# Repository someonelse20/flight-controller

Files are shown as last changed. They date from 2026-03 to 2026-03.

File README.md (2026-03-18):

# Custom Flight Controller

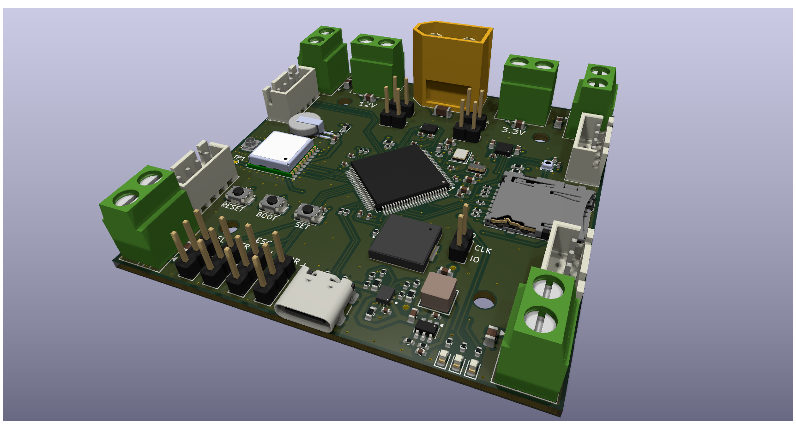
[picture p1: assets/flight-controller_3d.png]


A custom flight controller with IMU sensors for orientation, a GPS module, a Micro SD card slot, and support for my LoRa Transceiver module for telemetry along with a custom flight controller algorithm.
I built this for my project of creating a custom drone from scratch. 

## Usage
To use plug in a 3 cell lipo battery into the XT60 connector and attach the ESCs to the 4 corner screw terminals. Then plug in the ESC headers into the coresponding ESC headers on the board. 
Make sure a GPS antenna is connected to the U.FL connector. Plug in my transceiver module into any of the UART headers.
A Micro SD card is not strictly required but if inserted the board will log data and error logs. 

## Project Images
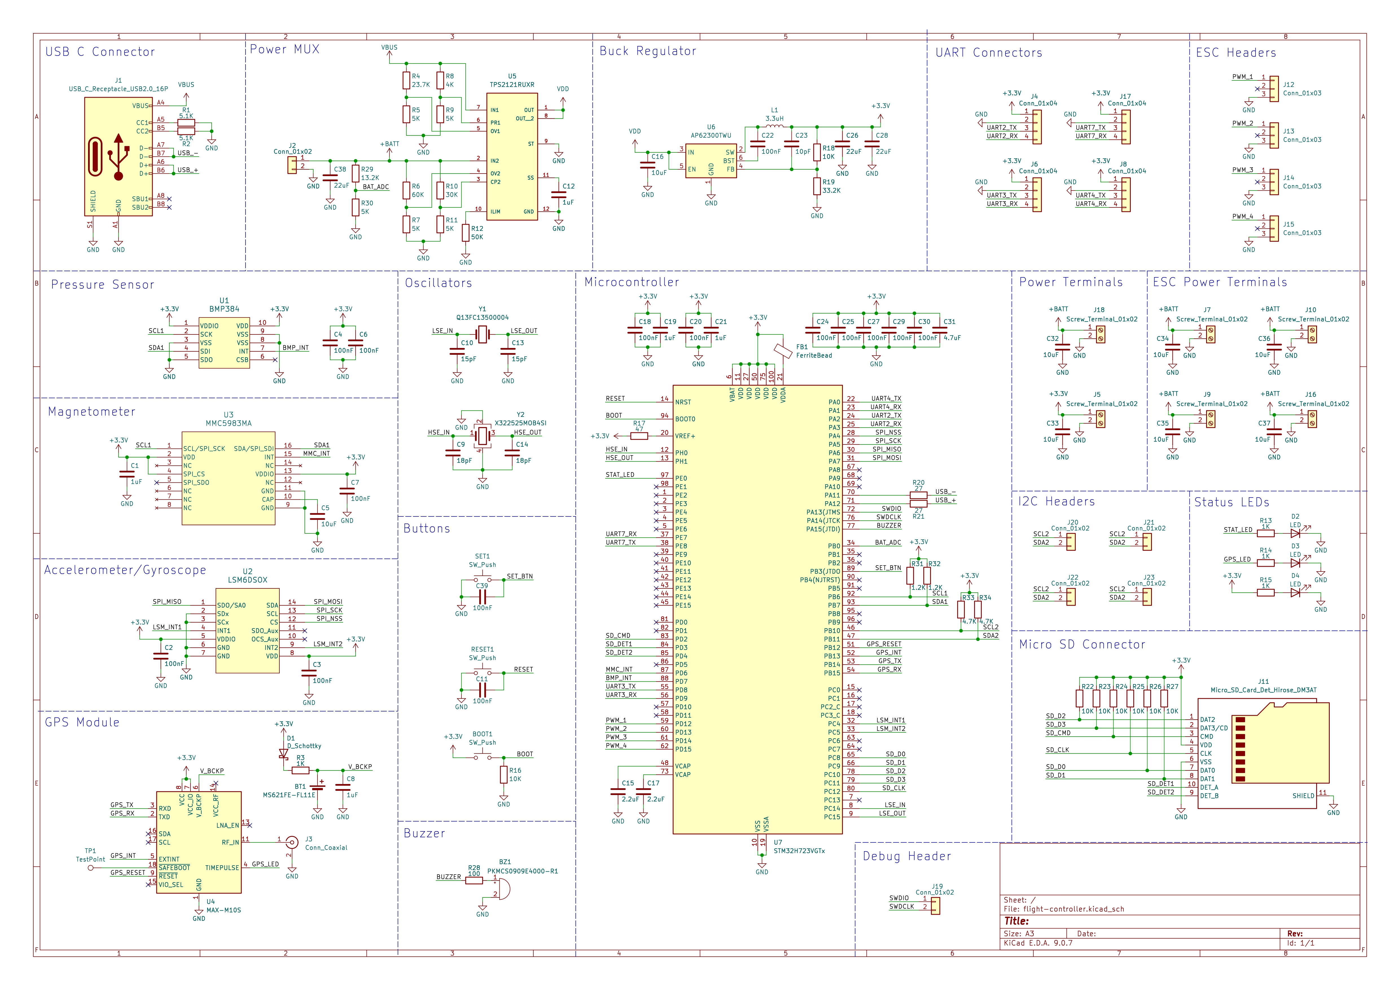
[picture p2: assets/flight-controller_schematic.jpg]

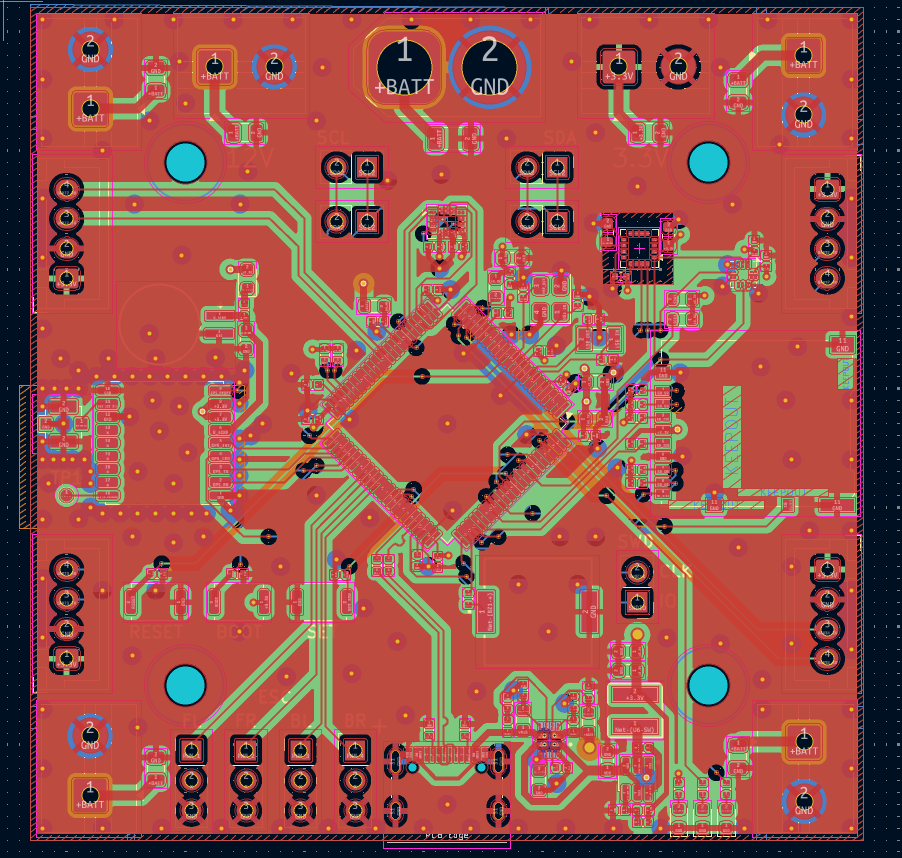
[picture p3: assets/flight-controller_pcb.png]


## BOM
The full BOM from digikey is in the digikey-bom.csv file in production.

| PCB Assembly | JLCPCB  | 96.10 | https://jlcpcb.com |
|---|---|---|---|
| Hand Soldered Parts | Digikey | 67.30 | https://www.digikey.com/en/mylists/list/OHMGL71TDV |

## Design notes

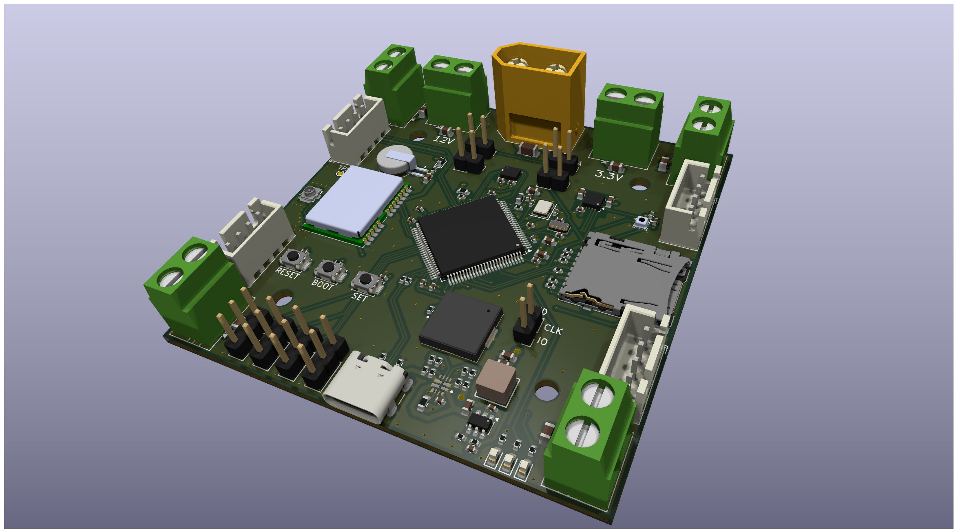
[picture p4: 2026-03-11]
hardware/flight-controller-3d.png

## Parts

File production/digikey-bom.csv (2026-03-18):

Index | Manufacturer Part Number | Manufacturer Name | Description | Quantity | Product Link
1 | MS621FE-FL11E | Seiko Instruments | BATT LITHIUM 3V 5.5MAH COIN | 2 | https://www.digikey.com/en/products/detail/seiko-instruments/MS621FE-FL11E/1889208
2 | MAX-M10S-00B | u-blox | GNSS LCC RX, ROM, TCXO, LNA, SAW | 2 | https://www.digikey.com/en/products/detail/u-blox/MAX-M10S-00B/15712906
3 | 691137710002 | Würth Elektronik | TERM BLK 2POS SIDE ENTRY 5MM PCB | 10 | https://www.digikey.com/en/products/detail/w%C3%BCrth-elektronik/691137710002/6644051
4 | FIT0587 | DFRobot | HIGH QUALITY GOLD PLATED XT60 MA | 2 | https://www.digikey.com/en/products/detail/dfrobot/FIT0587/9559256
5 | LSM6DSOXTR | STMicroelectronics | INEMO INERTIAL MODULE: 3D ACCELE | 2 | https://www.digikey.com/en/products/detail/stmicroelectronics/LSM6DSOXTR/9841882
6 | MMC5983MA | Memsic Inc. | SEN MR I2C/SPI 16-LGA | 2 | https://www.digikey.com/en/products/detail/memsic-inc/MMC5983MA/10452795
7 | BMP384 | Bosch Sensortec | SENSOR 18.13PSIA 10LGA | 2 | https://www.digikey.com/en/products/detail/bosch-sensortec/BMP384/13681277
8 | U.FL-R-SMT-1(10) | Hirose Electric Co Ltd | CONN U.FL RCPT STR 50 OHM SMD | 2 | https://www.digikey.com/en/products/detail/hirose-electric-co-ltd/U-FL-R-SMT-1-10/2391570
9 | B4B-XH-A | JST Sales America Inc. | CONN HEADER VERT 4POS 2.5MM | 10 | https://www.digikey.com/en/products/detail/jst-sales-america-inc/B4B-XH-A/1651047
10 | FXUB66.07.0150C | Taoglas Limited | RF ANT 3.4GHZ FLAT PATCH U.FL | 2 | https://www.digikey.com/en/products/detail/taoglas-limited/FXUB66-07-0150C/3724559

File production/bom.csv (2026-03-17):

Designator | Footprint | Quantity | Value | LCSC Part #
BOOT1, RESET1, SET1 | SW_Push_SPST_NO_Alps_SKRK | 3 | SW_Push
BT1 | BAT_MS621FE-FL11E | 1 | MS621FE-FL11E
BZ1 | SPKR_PKMCS0909E4000-R1 | 1 | PKMCS0909E4000-R1
C1, C19, C21, C8 | 0603 | 4 | 1uF
C10, C13 | 0402 | 2 | 15pF
C11, C18, C2, C20, C22, C24, C25, C27, C29, C3, C30, C39, C4, C6, C7 | 0402 | 15 | 100nF
C12 | 0402 | 1 | 1uF
C14, C9 | 0402 | 2 | 18pF
C15, C17 | 0402 | 2 | 2.2uF
C16, C5 | 0603 | 2 | 10uF
C23 | 0402 | 1 | 10pF
C26, C28 | 0603 | 2 | 22uF
C31 | 0603 | 1 | 4.7uF
C32, C33, C34, C35, C36, C37 | 0805 | 6 | 10uF
C38 | 1206 | 1 | 22uF
D1 | 0603 | 1 | D_Schottky
D2, D3 | 0603 | 2 | LED
D4 | 0603 | 1 | LED
FB1 | 0603 | 1 | FerriteBead
J1 | USB_C_Receptacle_GCT_USB4105-xx-A_16P_TopMnt_Horizontal | 1 | USB_C_Receptacle_USB2.0_16P
J10, J16, J18, J5, J7, J9 | TerminalBlock_MaiXu_MX126-5.0-02P_1x02_P5.00mm | 6 | Screw_Terminal_01x02
J11 | microSD_HC_Hirose_DM3AT-SF-PEJM5 | 1 | Micro_SD_Card_Det_Hirose_DM3AT
J12, J13, J14, J15 | PinHeader_1x03_P2.54mm_Vertical | 4 | Conn_01x03
J17, J4, J6, J8 | JST_XH_B4B-XH-A_1x04_P2.50mm_Vertical | 4 | Conn_01x04
J19, J20, J21, J22, J23 | PinHeader_1x02_P2.54mm_Vertical | 5 | Conn_01x02
J2 | AMASS_XT60-M_1x02_P7.20mm_Vertical | 1 | Conn_01x02
J3 | U.FL_Molex_MCRF_73412-0110_Vertical | 1 | Conn_Coaxial
L1 | IND_SRP4030FA_BRN | 1 | 3.3uH
R1, R2 | 0402 | 2 | 5.1K
R10 | 0402 | 1 | 30K
R11, R30, R5, R7, R9 | 0402 | 5 | 5K
R12 | 0603 | 1 | 50K
R13, R14, R15, R3 | 0402 | 4 | 1K
R16, R18, R22, R23, R24, R25, R26, R27 | 0402 | 8 | 10K
R17 | 0402 | 1 | 47
R19 | 0402 | 1 | 33.2K
R20, R21 | 0402 | 2 | 27
R28 | 0402 | 1 | 100
R29 | 0603 | 1 | 13.2K
R31, R32 | 0603 | 2 | 1.2K
R33, R34 | 0402 | 2 | 4.7K
R4 | 0402 | 1 | 23.7K
R6 | 0603 | 1 | 60K
R8 | 0603 | 1 | 4K
U1 | Rohm_MLGA010V020A_LGA-10_2x2mm_P0.45mm_LayoutBorder2x3y | 1 | BMP384
U2 | LGA-14_3x2.5mm_P0.5mm_LayoutBorder3x4y | 1 | LSM6DSOTR
U3 | LGA-16_3x3mm_P0.5mm | 1 | MMC5983MA
U4 | ublox_MAX | 1 | MAX-M10S
U5 | IC_TPS2121RUXR | 1 | TPS2121RUXR
U6 | TSOT-23-6 | 1 | AP62300TWU
U7 | LQFP-100_14x14mm_P0.5mm | 1 | STM32H723VGTx
Y1 | Crystal_SMD_3215-2Pin_3.2x1.5mm | 1 | Q13FC13500004
Y2 | Crystal_SMD_3225-4Pin_3.2x2.5mm | 1 | X322525MOB4SI

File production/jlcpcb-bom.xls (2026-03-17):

JLCPCB BOM Tool - BOM Matching
BOM name：jlcpcb-bom-JLCPCB Assembly Order.xlsx |  |  | Download Time：2026-03-18 00:47:03 |  |  |  | * Our matching results are updated in real-time, but stock and prices may change. If it's been over 24 hours, please re-match before placing your order.
PCB Assembled Qty：5 |  |  | Est. Total Price：25.3142
Your BOM |  |  |  |  | Matched Parts |  |  |  |  |  |  | Order Information
Top Designator | Bottom Designator | Comment | Footprint | JLCPCB Part # | Matches | Part # | Manufacturer | Footprint | Description | Category | Warning | JLCPCB Part # | Product link | Lib Type | Qty | Source | Total Price ($)
BOOT1,RESET1,SET1 |  | SW_Push | SMD,4x3mm |  | Unconfirmed | TS-1088-AR02016 | XUNPU | SMD,4x3mm | -30℃~+80℃ 1.6N 100,000 cycles 12V 2mm 3mm 4mm 50mA Black Round Button SMD(SMT) Tab SPST Surface Mount,Vertical Without Bracket SMD,4x3mm Tactile Switches ROHS | Tactile Switches | 1.There may be multiple types of parts, but one type of part has been matched. Please check.; | C720477 | https://jlcpcb.com/partdetail/XUNPU-TS_1088AR02016/C720477 | Basic | 6 | 6 JLCPCB | 0.3252
BZ1 |  | PKMCS0909E4000-R1 | - |  | Select by System | PKMCS0909E4000-R1 | Murata Electronics | - | -40℃~+85℃ 1.9mm 12.5V 4kHz 65dB 9mm 9mm Passive (Externally Driven) Piezoelectric - Buzzers ROHS | Buzzers |  | C910763 | https://jlcpcb.com/partdetail/MurataElectronics-PKMCS0909E4000R1/C910763 | Extended | 2 | 2 JLCPCB | 1.5874
C1,C19,C21,C8 |  | 1uF | 0603 |  | Select by System | CL10A105KB8NNNC | Samsung Electro-Mechanics | 0603 | 1uF 50V X5R ±10% 0603 Multilayer Ceramic Capacitors MLCC - SMD/SMT ROHS | Multilayer Ceramic Capacitors MLCC - SMD/SMT |  | C15849 | https://jlcpcb.com/partdetail/16531-CL10A105KB8NNNC/C15849 | Basic | 8 | 8 JLCPCB | 0.0576
C10,C13 |  | 15pF | 0402 |  | Select by System | 0402CG150J500NT | FH (Guangdong Fenghua Advanced Tech) | 0402 | 15pF 50V C0G ±5% 0402 Multilayer Ceramic Capacitors MLCC - SMD/SMT ROHS | Multilayer Ceramic Capacitors MLCC - SMD/SMT |  | C1548 | https://jlcpcb.com/partdetail/1900-0402CG150J500NT/C1548 | Basic | 4 | 4 JLCPCB | 0.0052
C11,C18,C2,C20,C22,C24,C25,C27,C29,C3,C30,C39,C4,C6,C7 |  | 100nF | 0402 |  | Select by System | CL05B104KO5NNNC | Samsung Electro-Mechanics | 0402 | 100nF 16V X7R ±10% 0402 Multilayer Ceramic Capacitors MLCC - SMD/SMT ROHS | Multilayer Ceramic Capacitors MLCC - SMD/SMT |  | C1525 | https://jlcpcb.com/partdetail/1877-CL05B104KO5NNNC/C1525 | Basic | 30 | 30 JLCPCB | 0.039
C12 |  | 1uF | 0402 |  | Select by System | CL05A105KA5NQNC | Samsung Electro-Mechanics | 0402 | 1uF 25V X5R ±10% 0402 Multilayer Ceramic Capacitors MLCC - SMD/SMT ROHS | Multilayer Ceramic Capacitors MLCC - SMD/SMT |  | C52923 | https://jlcpcb.com/partdetail/53938-CL05A105KA5NQNC/C52923 | Basic | 2 | 2 JLCPCB | 0.0082
C14,C9 |  | 18pF | 0402 |  | Select by System | 0402CG180J500NT | FH (Guangdong Fenghua Advanced Tech) | 0402 | 18pF 50V C0G ±5% 0402 Multilayer Ceramic Capacitors MLCC - SMD/SMT ROHS | Multilayer Ceramic Capacitors MLCC - SMD/SMT |  | C1549 | https://jlcpcb.com/partdetail/1901-0402CG180J500NT/C1549 | Basic | 4 | 4 JLCPCB | 0.0048
C15,C17 |  | 2.2uF | 0402 |  | Select by System | CL05A225MQ5NSNC | Samsung Electro-Mechanics | 0402 | 2.2uF 6.3V X5R ±20% 0402 Multilayer Ceramic Capacitors MLCC - SMD/SMT ROHS | Multilayer Ceramic Capacitors MLCC - SMD/SMT |  | C12530 | https://jlcpcb.com/partdetail/13164-CL05A225MQ5NSNC/C12530 | Basic | 4 | 4 JLCPCB | 0.0104
C16,C5 |  | 10uF | 0603 |  | Select by System | CL10A106KP8NNNC | Samsung Electro-Mechanics | 0603 | 10V 10uF X5R ±10% 0603 Multilayer Ceramic Capacitors MLCC - SMD/SMT ROHS | Multilayer Ceramic Capacitors MLCC - SMD/SMT |  | C19702 | https://jlcpcb.com/partdetail/20411-CL10A106KP8NNNC/C19702 | Basic | 4 | 4 JLCPCB | 0.0288
C23 |  | 10pF | 0402 |  | Select by System | CL05C100JB5NNNC | Samsung Electro-Mechanics | 0402 | 10pF 50V C0G ±5% 0402 Multilayer Ceramic Capacitors MLCC - SMD/SMT ROHS | Multilayer Ceramic Capacitors MLCC - SMD/SMT |  | C32949 | https://jlcpcb.com/partdetail/33914-CL05C100JB5NNNC/C32949 | Basic | 2 | 2 JLCPCB | 0.009
C26,C28 |  | 22uF | 0603 |  | Select by System | CL10A226MQ8NRNC | Samsung Electro-Mechanics | 0603 | 22uF 6.3V X5R ±20% 0603 Multilayer Ceramic Capacitors MLCC - SMD/SMT ROHS | Multilayer Ceramic Capacitors MLCC - SMD/SMT |  | C59461 | https://jlcpcb.com/partdetail/60514-CL10A226MQ8NRNC/C59461 | Basic | 4 | 4 JLCPCB | 0.0376
C31 |  | 4.7uF | 0603 |  | Select by System | CL10A475KO8NNNC | Samsung Electro-Mechanics | 0603 | 16V 4.7uF X5R ±10% 0603 Multilayer Ceramic Capacitors MLCC - SMD/SMT ROHS | Multilayer Ceramic Capacitors MLCC - SMD/SMT |  | C19666 | https://jlcpcb.com/partdetail/20375-CL10A475KO8NNNC/C19666 | Basic | 2 | 2 JLCPCB | 0.0206
C32,C33,C34,C35,C36,C37 |  | 10uF | 0805 |  | Select by System | GRM21BR61H106KE43L | Murata Electronics | 0805 | 10uF 50V X5R ±10% 0805 Multilayer Ceramic Capacitors MLCC - SMD/SMT ROHS | Multilayer Ceramic Capacitors MLCC - SMD/SMT |  | C440198 | https://jlcpcb.com/partdetail/439567-GRM21BR61H106KE43L/C440198 | Basic | 12 | 12 JLCPCB | 0.8604
C38 |  | 22uF | 1206 |  | Select by System | CL31A226KAHNNNE | Samsung Electro-Mechanics | 1206 | 22uF 25V X5R ±10% 1206 Multilayer Ceramic Capacitors MLCC - SMD/SMT ROHS | Multilayer Ceramic Capacitors MLCC - SMD/SMT |  | C12891 | https://jlcpcb.com/partdetail/13537-CL31A226KAHNNNE/C12891 | Basic | 2 | 2 JLCPCB | 0.0946
D1 |  | D_Schottky | 0603 |  | Select by System | SD0603S040S0R2 | Kyocera AVX | 0603 | 1uA@40V 200mA 40V 450mV@200mA 0603 Schottky Diodes ROHS | Schottky Diodes |  | C143772 | https://jlcpcb.com/partdetail/KyoceraAVX-SD0603S040S0R2/C143772 | Extended | 5 | 5 JLCPCB | 0.8985
D2,D3 |  | LED | 0603 |  | Select by System | KT-0603W | Hubei KENTO Elec | 0603 | -40℃~+85℃ 100mW 120° 2.6V~3.1V 360mcd 5mA Discrete Diode Top-mount White Yellow Lens 0603 LED Indication - Discrete ROHS | LED Indication - Discrete |  | C2290 | https://jlcpcb.com/partdetail/Hubei_KENTOElec-KT0603W/C2290 | Basic | 4 | 4 JLCPCB | 0.0468
D4 |  | LED | 0603 |  | Select by System | KT-0603R | Hubei KENTO Elec | 0603 | -40℃~+85℃ 120° 2.4V 20mA 300mcd 40mW 615nm~630nm 645nm Discrete Diode Red Water Clear 0603 LED Indication - Discrete ROHS | LED Indication - Discrete |  | C2286 | https://jlcpcb.com/partdetail/Hubei_KENTOElec-KT0603R/C2286 | Basic | 2 | 2 JLCPCB | 0.013
FB1 |  | FerriteBead | 0603 |  | Select by System | GZ1608D601TF | Sunlord | 0603 | -55℃~+125℃ 1 200mA 450mΩ 600Ω@100MHz ±25% 0603 Ferrite Beads ROHS | Ferrite Beads |  | C1002 | https://jlcpcb.com/partdetail/Sunlord-GZ1608D601TF/C1002 | Basic | 2 | 2 JLCPCB | 0.0264
J1 |  | USB_C_Receptacle_USB2.0_16P | SMD |  | Select by System | TYPE-C-31-M-12 | Korean Hroparts Elec | SMD | -30℃~+80℃ 1 10,000 cycles 16P 20V 5A 7.35mm Female Surface Mount, Right Angle Type-C SMD USB Connectors ROHS | USB Connectors |  | C165948 | https://jlcpcb.com/partdetail/Korean_HropartsElec-TYPE_C_31_M12/C165948 | Extended | 2 | 2 JLCPCB | 0.3632
J11 |  | Micro_SD_Card_Det_Hirose_DM3AT | SMD |  | Select by System | DM3AT-SF-PEJM5 | HRS(Hirose) | SMD | -25℃~+85℃ 1.68mm Connector and Ejector MicroSD Card (TF Card) No Push-Push SMD SD Card / Memory Card Connector ROHS | SD Card / Memory Card Connector |  | C114218 | https://jlcpcb.com/partdetail/HRS_Hirose-DM3AT_SFPEJM5/C114218 | Extended | 2 | 2 JLCPCB | 2.7756
L1 |  | 3.3uH | SMD,4x4mm |  | Select by System | SWPA4030S3R3MT | Sunlord | SMD,4x4mm | 2.4A 3.3uH 3.6A 52mΩ ±20% SMD,4x4mm Power Inductors ROHS | Power Inductors |  | C15269 | https://jlcpcb.com/partdetail/Sunlord-SWPA4030S3R3MT/C15269 | Extended | 6 | 6 JLCPCB | 0.4842
R1,R2 |  | 5.1K | 0402 |  | Select by System | 0402WGF5101TCE | UNI-ROYAL(Uniroyal Elec) | 0402 | -55℃~+155℃ 5.1kΩ 50V 62.5mW Thick Film Resistor ±1% ±100ppm/℃ 0402 Chip Resistor - Surface Mount ROHS | Chip Resistor - Surface Mount |  | C25905 | https://jlcpcb.com/partdetail/26648-0402WGF5101TCE/C25905 | Basic | 4 | 4 JLCPCB | 0.0032
R4 |  | 23.7K | 0402 |  | Select by System | 0402WGF2372TCE | UNI-ROYAL(Uniroyal Elec) | 0402 | -55℃~+155℃ 23.7kΩ 50V 62.5mW Thick Film Resistor ±1% ±100ppm/℃ 0402 Chip Resistor - Surface Mount ROHS | Chip Resistor - Surface Mount |  | C82134 | https://jlcpcb.com/partdetail/83289-0402WGF2372TCE/C82134 | Extended | 20 | 20 JLCPCB | 0.014
R6 |  | 60K | 0603 |  | Select by System | RT0603BRD0760KL | YAGEO | 0603 | -55℃~+155℃ 100mW 60kΩ 75V Thin Film Resistor ±0.1% ±25ppm/℃ 0603 Chip Resistor - Surface Mount ROHS | Chip Resistor - Surface Mount |  | C6460576 | https://jlcpcb.com/partdetail/YAGEO-RT0603BRD0760KL/C6460576 | Extended | 20 | 20 JLCPCB | 0.526
R8 |  | 4K | 0603 |  | Select by System | ARG03FTC4001N | Viking Tech | 0603 | -55℃~+155℃ 100mW 4kΩ 75V Thin Film Resistor ±1% ±25ppm/℃ 0603 Chip Resistor - Surface Mount ROHS | Chip Resistor - Surface Mount |  | C2984443 | https://jlcpcb.com/partdetail/VikingTech-ARG03FTC4001N/C2984443 | Extended | 20 | 20 JLCPCB | 0.168
R10 |  | 30K | 0402 |  | Select by System | FRC0402F3002TS | FOJAN | 0402 | -55℃~+155℃ 30kΩ 50V 62.5mW Thick Film Resistor ±1% ±100ppm/℃ 0402 Chip Resistor - Surface Mount ROHS | Chip Resistor - Surface Mount |  | C2909347 | https://jlcpcb.com/partdetail/FOJAN-FRC0402F3002TS/C2909347 | Extended | 20 | 20 JLCPCB | 0.012
R11,R30,R5,R7,R9 |  | 5K | 0402 |  | Select by System | RC0402FR-075KL | YAGEO | 0402 | -55℃~+155℃ 50V 5kΩ 62.5mW Thick Film Resistor ±1% ±100ppm/℃ 0402 Chip Resistor - Surface Mount ROHS | Chip Resistor - Surface Mount |  | C477765 | https://jlcpcb.com/partdetail/YAGEO-RC0402FR075KL/C477765 | Extended | 20 | 20 JLCPCB | 0.016
R12 |  | 50K | 0603 |  | Select by System | RT0603BRD0750KL | YAGEO | 0603 | -55℃~+155℃ 100mW 50kΩ 75V Thin Film Resistor ±0.1% ±25ppm/℃ 0603 Chip Resistor - Surface Mount ROHS | Chip Resistor - Surface Mount |  | C861451 | https://jlcpcb.com/partdetail/YAGEO-RT0603BRD0750KL/C861451 | Extended | 20 | 20 JLCPCB | 0.488
R13,R14,R15,R3 |  | 1K | 0402 |  | Select by System | 0402WGF1001TCE | UNI-ROYAL(Uniroyal Elec) | 0402 | -55℃~+155℃ 1kΩ 50V 62.5mW Thick Film Resistor ±1% ±100ppm/℃ 0402 Chip Resistor - Surface Mount ROHS | Chip Resistor - Surface Mount |  | C11702 | https://jlcpcb.com/partdetail/12256-0402WGF1001TCE/C11702 | Basic | 8 | 8 JLCPCB | 0.0056
R16,R18,R22,R23,R24,R25,R26,R27 |  | 10K | 0402 |  | Select by System | 0402WGF1002TCE | UNI-ROYAL(Uniroyal Elec) | 0402 | -55℃~+155℃ 10kΩ 50V 62.5mW Thick Film Resistor ±1% ±100ppm/℃ 0402 Chip Resistor - Surface Mount ROHS | Chip Resistor - Surface Mount |  | C25744 | https://jlcpcb.com/partdetail/26487-0402WGF1002TCE/C25744 | Basic | 16 | 16 JLCPCB | 0.0128
R17 |  | 47 | 0402 |  | Select by System | 0402WGF470JTCE | UNI-ROYAL(Uniroyal Elec) | 0402 | -55℃~+155℃ 47Ω 50V 62.5mW Thick Film Resistor ±1% ±100ppm/℃ 0402 Chip Resistor - Surface Mount ROHS | Chip Resistor - Surface Mount |  | C25118 | https://jlcpcb.com/partdetail/25861-0402WGF470JTCE/C25118 | Extended | 20 | 20 JLCPCB | 0.016
R19 |  | 33.2K | 0402 |  | Select by System | FRC0402F3322TS | FOJAN | 0402 | -55℃~+155℃ 33.2kΩ 50V 62.5mW Thick Film Resistor ±1% ±100ppm/℃ 0402 Chip Resistor - Surface Mount ROHS | Chip Resistor - Surface Mount |  | C2930001 | https://jlcpcb.com/partdetail/FOJAN-FRC0402F3322TS/C2930001 | Extended | 20 | 20 JLCPCB | 0.012
R20,R21 |  | 27 | 0402 |  | Select by System | 0402WGF270JTCE | UNI-ROYAL(Uniroyal Elec) | 0402 | -55℃~+155℃ 27Ω 50V 62.5mW Thick Film Resistor ±1% ±100ppm/℃ 0402 Chip Resistor - Surface Mount ROHS | Chip Resistor - Surface Mount |  | C25100 | https://jlcpcb.com/partdetail/25843-0402WGF270JTCE/C25100 | Extended | 20 | 20 JLCPCB | 0.016
R28 |  | 100 | 0402 |  | Select by System | 0402WGF1000TCE | UNI-ROYAL(Uniroyal Elec) | 0402 | -55℃~+155℃ 100Ω 50V 62.5mW Thick Film Resistor ±1% ±100ppm/℃ 0402 Chip Resistor - Surface Mount ROHS | Chip Resistor - Surface Mount |  | C25076 | https://jlcpcb.com/partdetail/25819-0402WGF1000TCE/C25076 | Basic | 2 | 2 JLCPCB | 0.0016
R29 |  | 13.2K | 0603 |  | Select by System | RT0603BRD0713K2L | YAGEO | 0603 | -55℃~+155℃ 100mW 13.2kΩ 75V Thin Film Resistor ±0.1% ±25ppm/℃ 0603 Chip Resistor - Surface Mount ROHS | Chip Resistor - Surface Mount |  | C861116 | https://jlcpcb.com/partdetail/YAGEO-RT0603BRD0713K2L/C861116 | Extended | 20 | 20 JLCPCB | 0.518
R31,R32 |  | 1.2K | 0603 |  | Select by System | 0603WAF1201T5E | UNI-ROYAL(Uniroyal Elec) | 0603 | -55℃~+155℃ 1.2kΩ 100mW 75V Thick Film Resistor ±1% ±100ppm/℃ 0603 Chip Resistor - Surface Mount ROHS | Chip Resistor - Surface Mount |  | C22765 | https://jlcpcb.com/partdetail/23492-0603WAF1201T5E/C22765 | Basic | 4 | 4 JLCPCB | 0.0068
R33,R34 |  | 4.7K | 0402 |  | Select by System | 0402WGF4701TCE | UNI-ROYAL(Uniroyal Elec) | 0402 | -55℃~+155℃ 4.7kΩ 50V 62.5mW Thick Film Resistor ±1% ±100ppm/℃ 0402 Chip Resistor - Surface Mount ROHS | Chip Resistor - Surface Mount |  | C25900 | https://jlcpcb.com/partdetail/26643-0402WGF4701TCE/C25900 | Basic | 4 | 4 JLCPCB | 0.0032
U1 |  | BMP384 | LGA-10(2x2) |  | Select by System | BMP384 | Bosch Sensortec | LGA-10(2x2) | -40℃~+85℃ 1.65V~3.6V 1pa/K 2uA 30Kpa~1.25bar 50pa 9pa I2C、SPI LGA-10(2x2) Pressure Sensors ROHS | Pressure Sensors |  | C5577555 | https://jlcpcb.com/partdetail/BoschSensortec-BMP384/C5577555 | Extended | 0 | 0 JLCPCB | 0
U2 |  | LSM6DSOTR | LGA-14(2.5x3) |  | Select by System | LSM6DSOTR | STMicroelectronics | LGA-14(2.5x3) | -40℃~+85℃ 1.71V~3.6V 9KB Accelerometer Gyroscope SPI、I2C X,Y,Z X,Y,Z ±16g ±2000dps LGA-14(2.5x3) Accelerometers ROHS | Accelerometers |  | C2655100 | https://jlcpcb.com/partdetail/STMicroelectronics-LSM6DSOTR/C2655100 | Extended | 0 | 0 JLCPCB | 0
U3 |  | MMC5983MA | LGA-16(3x3) |  | Select by System | MMC5983MA | MEMSIC | LGA-16(3x3) | -40℃~+105℃ 18bit 2.8V~3.6V 450uA I2C、SPI ±8Gs ±8Gs LGA-16(3x3) 3D Magnetic Sensors ROHS | 3D Magnetic Sensors |  | C404329 | https://jlcpcb.com/partdetail/MEMSIC-MMC5983MA/C404329 | Extended | 0 | 0 JLCPCB | 0
U5 |  | TPS2121RUXR | VQFN-HR-12(2x2.5) |  | Select by System | TPS2121RUXR | Texas Instruments | VQFN-HR-12(2x2.5) | -40℃~+125℃ 2.8V~22V 200uA 56mΩ VQFN-HR-12(2x2.5) ORing Controllers ROHS | Battery Management |  | C485916 | https://jlcpcb.com/partdetail/TexasInstruments-TPS2121RUXR/C485916 | Extended | 2 | 2 JLCPCB | 1.863
U6 |  | AP62300TWU | TSOT-26 |  | Select by System | AP62300TWU-7 | Diodes Incorporated | TSOT-26 | -40℃~+125℃ 1 155uA 3A 4.2V~18V 750kHz 763mV~7V Adjustable Buck Buck Built-in Yes TSOT-26 DC-DC Converters ROHS | DC-DC Converters |  | C1883519 | https://jlcpcb.com/partdetail/DiodesIncorporated-AP62300TWU7/C1883519 | Extended | 5 | 5 JLCPCB | 0.6515
U7 |  | STM32H723VGTx | LQFP-100(14x14) |  | Select by System | STM32H723VGT6 | STMicroelectronics | LQFP-100(14x14) | -40℃~+85℃ 1.71V~3.6V 12bit 16bit 1MB 32 Bit 550MHz 564KB 80 ARM Cortex-M7 Built-in FLASH LQFP-100(14x14) Microcontrollers (MCU/MPU/SOC) ROHS | Microcontrollers (MCU/MPU/SOC) |  | C730142 | https://jlcpcb.com/partdetail/STMicroelectronics-STM32H723VGT6/C730142 | Extended | 2 | 2 JLCPCB | 12.7872
Y1 |  | Q13FC13500004 | SMD3215-2P |  | Select by System | Q13FC13500004 | Seiko Epson | SMD3215-2P | -40℃~+85℃ 12.5pF 32.768kHz 70kΩ Crystal Oscillator ±20ppm SMD3215-2P Crystals ROHS | Crystals |  | C32346 | https://jlcpcb.com/partdetail/SeikoEpson-Q13FC13500004/C32346 | Basic | 2 | 2 JLCPCB | 0.3528
Y2 |  | X322525MOB4SI | SMD3225-4P |  | Select by System | X322525MOB4SI | YXC Crystal Oscillators | SMD3225-4P | -40℃~+85℃ 12pF 25MHz Crystal Oscillator ±10ppm ±20ppm SMD3225-4P Crystals ROHS | Crystals |  | C9006 | https://jlcpcb.com/partdetail/YXC_CrystalOscillators-X322525MOB4SI/C9006 | Basic | 2 | 2 JLCPCB | 0.144
BT1 |  | MS621FE-FL11E |  |  | No matches | No Part Selected
J2 |  | Conn_01x02 |  |  | No matches | No Part Selected
J3 |  | Conn_Coaxial |  |  | No matches | No Part Selected
J10,J16,J18,J5,J7,J9 |  | Screw_Terminal_01x02 |  |  | No matches | No Part Selected
J12,J13,J14,J15 |  | Conn_01x03 |  |  | No matches | No Part Selected
J17,J4,J6,J8 |  | Conn_01x04 |  |  | No matches | No Part Selected
J19,J20,J21,J22,J23 |  | Conn_01x02 |  |  | No matches | No Part Selected

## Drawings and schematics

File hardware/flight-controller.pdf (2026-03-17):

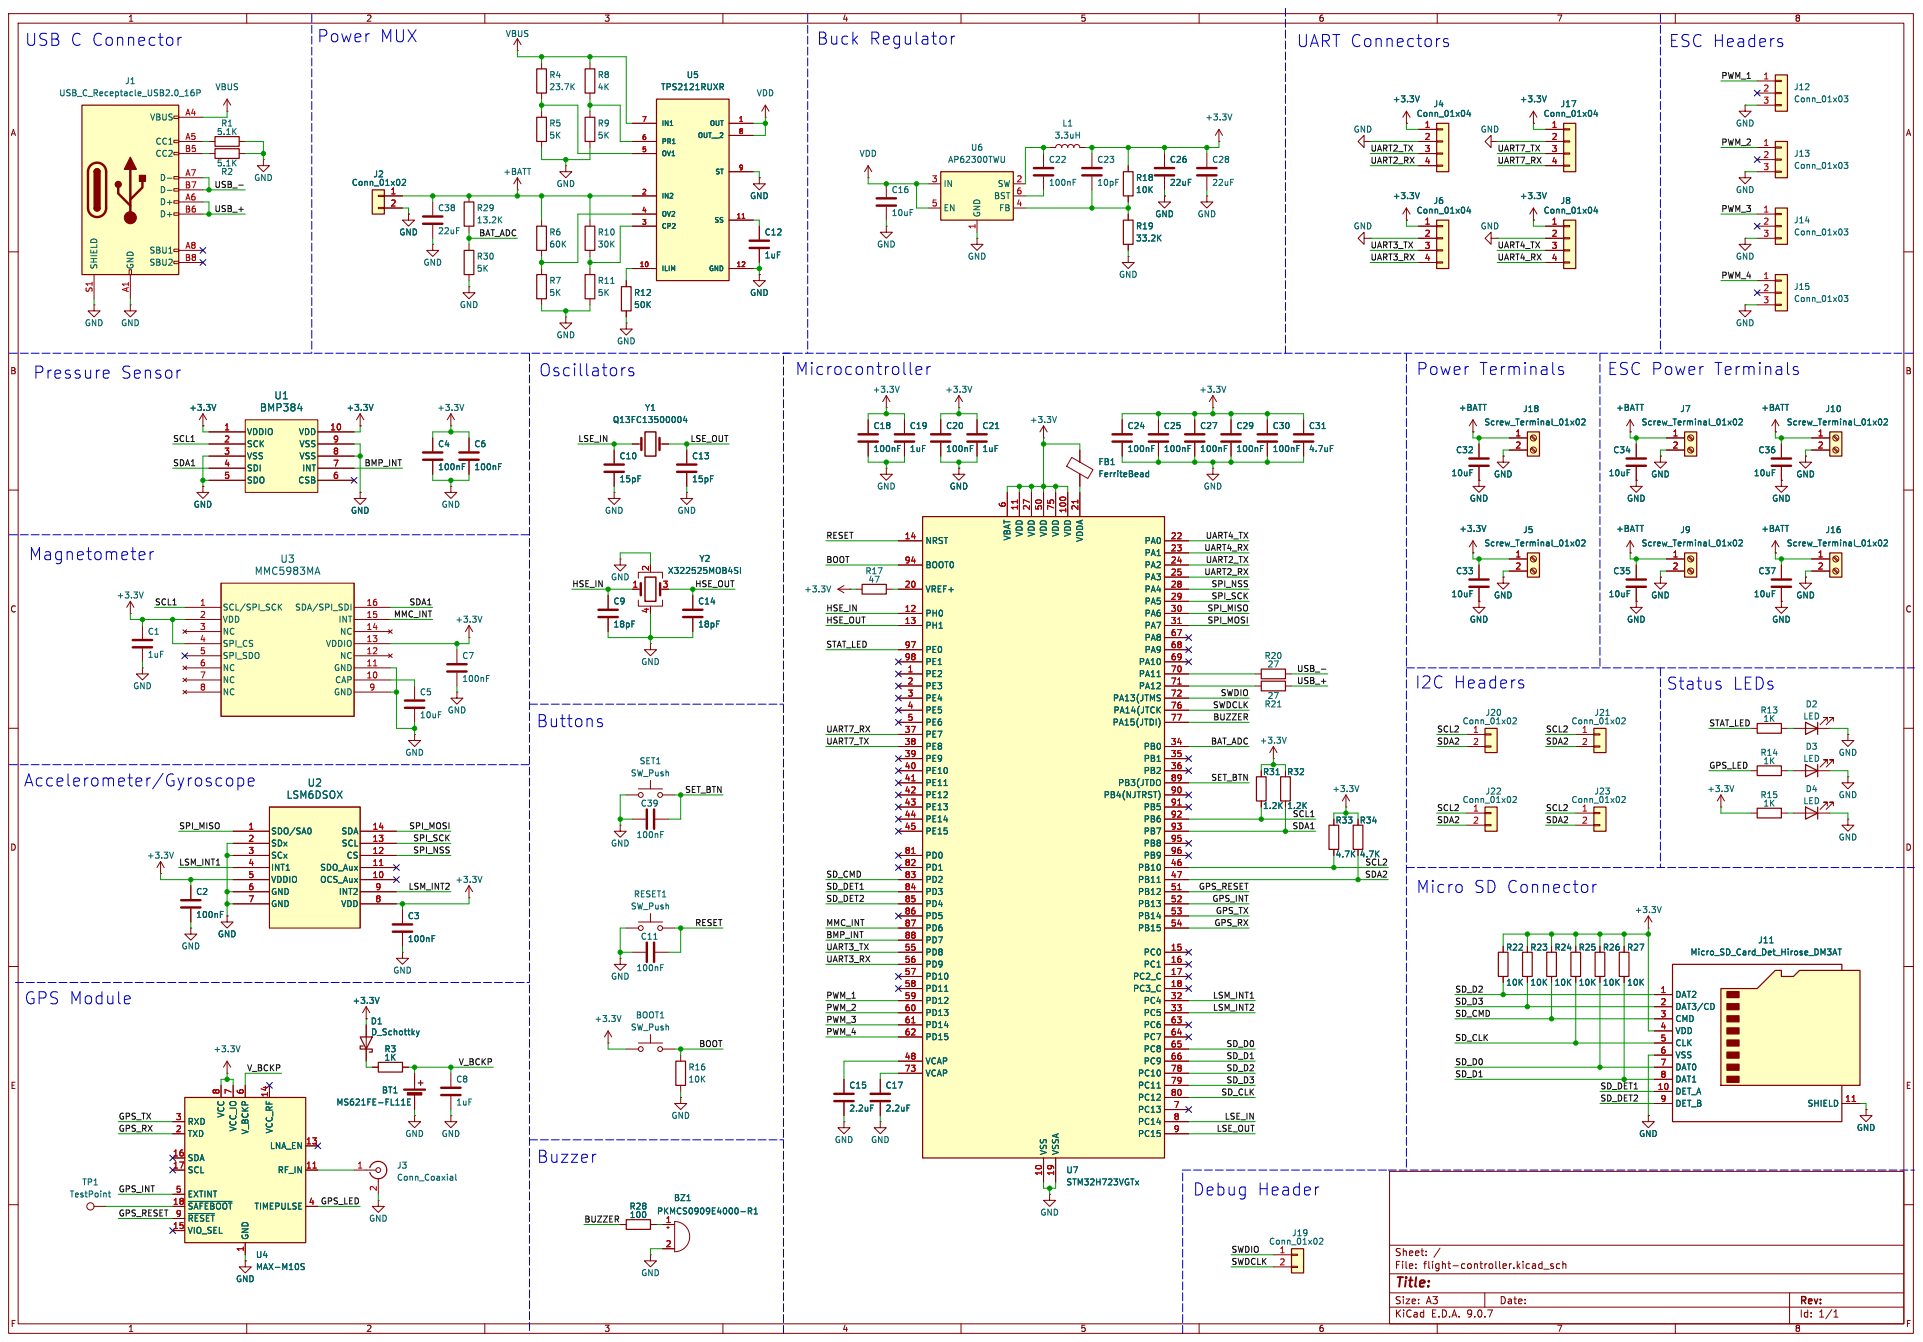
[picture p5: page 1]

6 VDD 11 VDD 27 VDD 50 VSS 10 VDD 75 VSSA 19 VDD 100 VDDA 21 PA0 22 PA1 23 PA2 24 PA3 25 PA4 28 PA5 29 PA6 30 PA7 31 PA8 67 PA9 68 PA10 69 PA11 70 PA12 71 PA13(JTMS 72 PA14(JTCK 76 PA15(JTDI) 77 PB0 34 PB1 35 PB2 36 PB3(JTDO 89 PB4(NJTRST) 90 PB5 91 PB6 92 PB7 93 PB8 95 PB9 96 PB10 46 PB11 47 PB12 51 PB13 52 PB14 53 PB15 54 PC0 15 PC1 16 PC2_C 17 PC3_C 18 PC4 32 PC5 33 PC6 63 PC7 64 PC8 65 PC9 66 PC10 78 PC11 79 PC12 80 PC13 7 PC14 8 PC15 9 U7STM32H723VGTx SDO/SA0 1 SDx 2 SCx 3

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

Id: 1/1 Title: File: flight-controller.kicad_sch Sheet: /

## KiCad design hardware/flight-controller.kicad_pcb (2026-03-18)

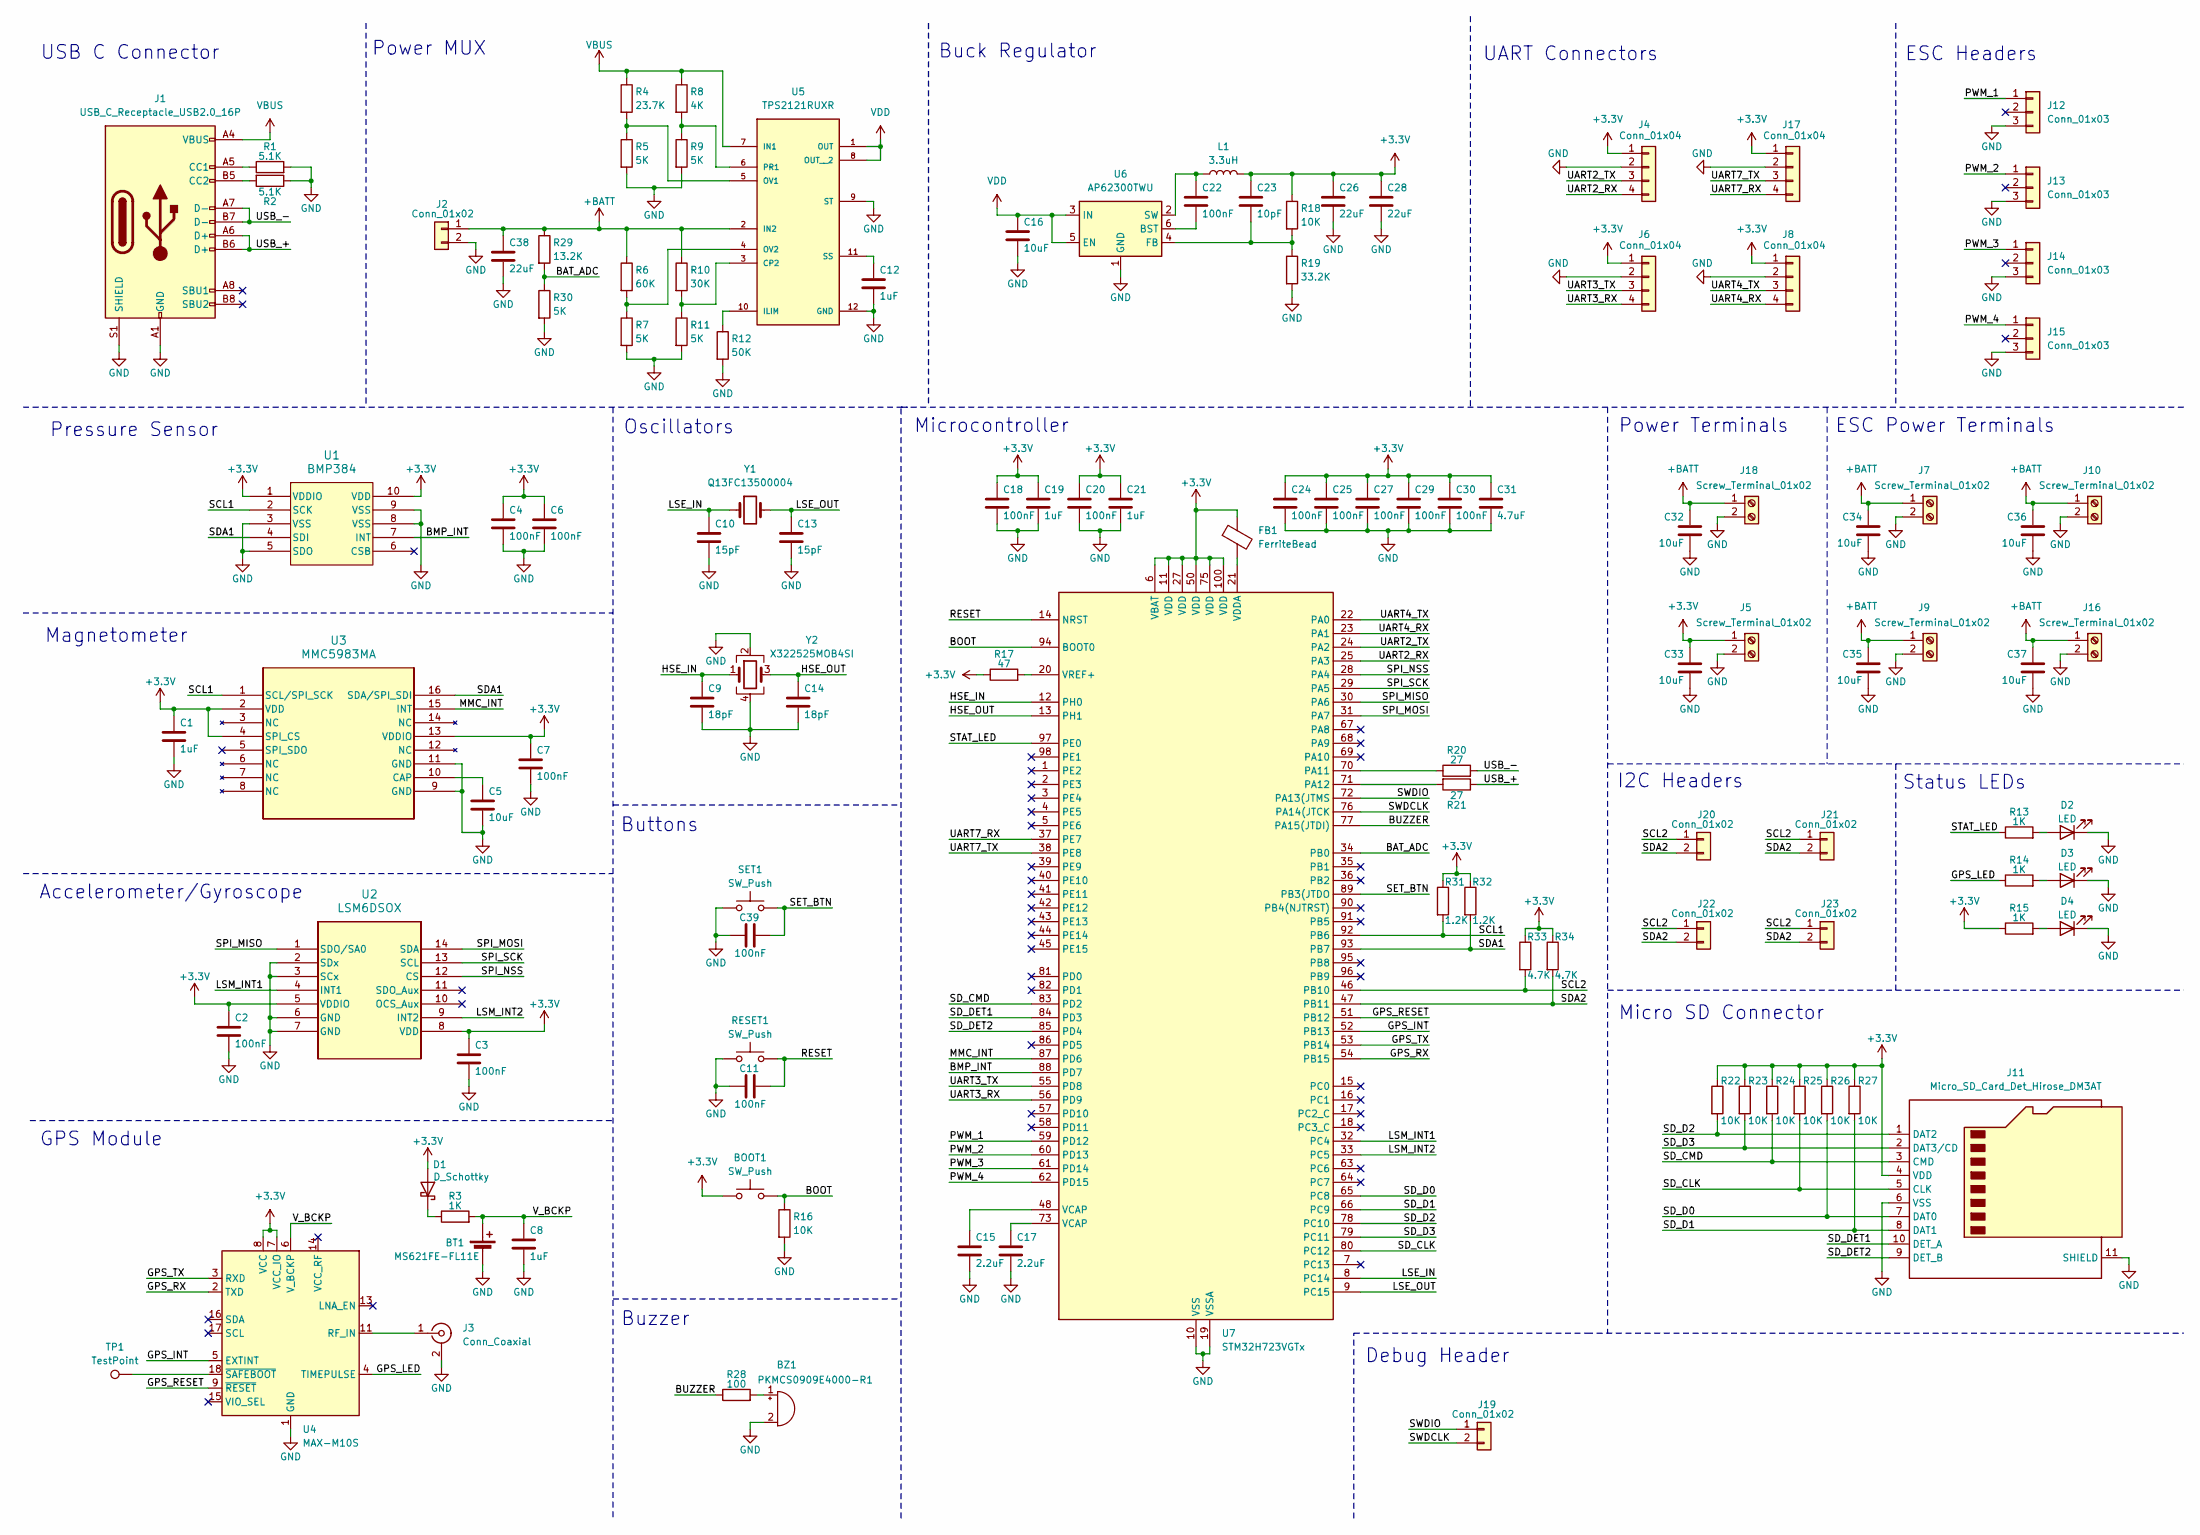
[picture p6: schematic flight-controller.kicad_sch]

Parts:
BOOT1: SW_Push; SW_Push_SPST_NO_Alps_SKRK
BT1: MS621FE-FL11E; BAT_MS621FE-FL11E
BZ1: PKMCS0909E4000-R1; SPKR_PKMCS0909E4000-R1
C1, C8, C19, C21: 1uF; C_0603_1608Metric
C2, C3, C4, C6, C7, C11, C18, C20, C22, C24, C25, C27, C29, C30, C39: 100nF; C_0402_1005Metric
C5, C16: 10uF; C_0603_1608Metric
C9, C14: 18pF; C_0402_1005Metric
C10, C13: 15pF; C_0402_1005Metric
C12: 1uF; C_0402_1005Metric
C15, C17: 2.2uF; C_0402_1005Metric
C23: 10pF; C_0402_1005Metric
C26, C28: 22uF; C_0603_1608Metric
C31: 4.7uF; C_0603_1608Metric
C32, C33, C34, C35, C36, C37: 10uF; C_0805_2012Metric
C38: 22uF; C_1206_3216Metric
D1: D_Schottky; D_0603_1608Metric
D2, D3, D4: LED; LED_0603_1608Metric
FB1: FerriteBead; L_0603_1608Metric
J1: USB_C_Receptacle_USB2.0_16P; USB_C_Receptacle_GCT_USB4105-xx-A_16P_TopMnt_Horizontal
J2: Conn_01x02; AMASS_XT60-M_1x02_P7.20mm_Vertical
J3: Conn_Coaxial; U.FL_Molex_MCRF_73412-0110_Vertical
J4, J6, J8, J17: Conn_01x04; JST_XH_B4B-XH-A_1x04_P2.50mm_Vertical
J5, J7, J9, J10, J16, J18: Screw_Terminal_01x02; TerminalBlock_MaiXu_MX126-5.0-02P_1x02_P5.00mm
J11: Micro_SD_Card_Det_Hirose_DM3AT; microSD_HC_Hirose_DM3AT-SF-PEJM5
J12, J13, J14, J15: Conn_01x03; PinHeader_1x03_P2.54mm_Vertical
J19, J20, J21, J22, J23: Conn_01x02; PinHeader_1x02_P2.54mm_Vertical
L1: 3.3uH; IND_SRP4030FA_BRN
R1, R2: 5.1K; R_0402_1005Metric
R3, R13, R14, R15: 1K; R_0402_1005Metric
R4: 23.7K; R_0402_1005Metric
R5, R7, R9, R11, R30: 5K; R_0402_1005Metric
R6: 60K; R_0603_1608Metric
R8: 4K; R_0603_1608Metric
R10: 30K; R_0402_1005Metric
R12: 50K; R_0603_1608Metric
R16, R18, R22, R23, R24, R25, R26, R27: 10K; R_0402_1005Metric
R17: 47; R_0402_1005Metric
R19: 33.2K; R_0402_1005Metric
R20, R21: 27; R_0402_1005Metric
R28: 100; R_0402_1005Metric
R29: 13.2K; R_0603_1608Metric
R31, R32: 1.2K; R_0603_1608Metric
R33, R34: 4.7K; R_0402_1005Metric
RESET1: SW_Push; SW_Push_SPST_NO_Alps_SKRK
SET1: SW_Push; SW_Push_SPST_NO_Alps_SKRK
TP1: TestPoint; TestPoint_Pad_D1.0mm
U1: BMP384; Rohm_MLGA010V020A_LGA-10_2x2mm_P0.45mm_LayoutBorder2x3y
U2: LSM6DSOX; LGA-14_3x2.5mm_P0.5mm_LayoutBorder3x4y
U3: MMC5983MA; LGA-16_3x3mm_P0.5mm
U4: MAX-M10S; ublox_MAX
U5: TPS2121RUXR; IC_TPS2121RUXR
U6: AP62300TWU; TSOT-23-6
U7: STM32H723VGTx; LQFP-100_14x14mm_P0.5mm
Y1: Q13FC13500004; Crystal_SMD_3215-2Pin_3.2x1.5mm
Y2: X322525MOB4SI; Crystal_SMD_3225-4Pin_3.2x2.5mm

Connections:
+3.3V: BOOT1.1, C1.1, C2.1, C3.1, C4.1, C6.1, C7.1, C18.1, C19.1, C20.1, C21.1, C23.1, C24.1, C25.1, C26.1, C27.1, C28.1, C29.1, C30.1, C31.1, C33.1, D1.2 (A), FB1.1, J4.1, J5.1, J6.1, J8.1, J11.4 (VDD), J17.1, L1.2, R15.1, R17.1, R18.1, R22.1, R23.1, R24.1, R25.1, R26.1, R27.1, R31.1, R32.1, R33.1, R34.1, U1.1 (VDDIO), U1.10 (VDD), U2.5 (VDDIO), U2.8 (VDD), U3.2 (VDD), U3.4 (SPI_CS), U3.13 (VDDIO), U4.7 (VCC_IO), U4.8 (VCC), U7.6 (VBAT), U7.11 (VDD), U7.27 (VDD), U7.50 (VDD), U7.75 (VDD), U7.100 (VDD); also elsewhere on the board
+BATT: C32.1, C34.1, C35.1, C36.1, C37.1, C38.1, J2.1, J7.1, J9.1, J10.1, J16.1, J18.1, R6.1, R10.1, R29.1, U5.2 (IN2)
/BAT_ADC: R29.2, R30.1, U7.34 (PB0)
/BMP_INT: U1.7 (INT), U7.88 (PD7)
/BOOT: BOOT1.2, R16.1, U7.94 (BOOT0)
/BUZZER: R28.1, U7.77 (PA15(JTDI))
/GPS_INT: U4.5 (EXTINT), U7.52 (PB13); also elsewhere on the board
/GPS_LED: R14.1, U4.4 (TIMEPULSE); also elsewhere on the board
/GPS_RESET: U4.9 (~RESET), U7.51 (PB12); also elsewhere on the board
/GPS_RX: U4.2 (TXD), U7.54 (PB15); also elsewhere on the board
/GPS_TX: U4.3 (RXD), U7.53 (PB14); also elsewhere on the board
/HSE_IN: C9.1, U7.12 (PH0), Y2.1
/HSE_OUT: C14.1, U7.13 (PH1), Y2.3
/LSE_IN: C10.1, U7.8 (PC14), Y1.1
/LSE_OUT: C13.1, U7.9 (PC15), Y1.2
/LSM_INT1: U2.4 (INT1), U7.32 (PC4)
/LSM_INT2: U2.9 (INT2), U7.33 (PC5)
/MMC_INT: U3.15 (INT), U7.87 (PD6)
/PWM_1: J12.1, U7.59 (PD12)
/PWM_2: J13.1, U7.60 (PD13)
/PWM_3: J14.1, U7.61 (PD14)
/PWM_4: J15.1, U7.62 (PD15)
/RESET: C11.2, RESET1.2, U7.14 (NRST)
/SCL1: R31.2, U1.2 (SCK), U3.1 (SCL/SPI_SCK), U7.92 (PB6)
/SCL2: J20.1, J21.1, J22.1, J23.1, R33.2, U7.46 (PB10)
/SDA1: R32.2, U1.4 (SDI), U3.16 (SDA/SPI_SDI), U7.93 (PB7)
/SDA2: J20.2, J21.2, J22.2, J23.2, R34.2, U7.47 (PB11)
/SD_CLK: J11.5 (CLK), R25.2, U7.80 (PC12)
/SD_CMD: J11.3 (CMD), R24.2, U7.83 (PD2)
/SD_D0: J11.7 (DAT0), R26.2, U7.65 (PC8)
/SD_D1: J11.8 (DAT1), R27.2, U7.66 (PC9)
/SD_D2: J11.1 (DAT2), R22.2, U7.78 (PC10)
/SD_D3: J11.2 (DAT3/CD), R23.2, U7.79 (PC11)
/SD_DET1: J11.10 (DET_A), U7.84 (PD3)
/SD_DET2: J11.9 (DET_B), U7.85 (PD4)
/SET_BTN: C39.2, SET1.2, U7.89 (PB3(JTDO)
/SPI_MISO: U2.1 (SDO/SA0), U7.30 (PA6)
/SPI_MOSI: U2.14 (SDA), U7.31 (PA7)
/SPI_NSS: U2.12 (CS), U7.28 (PA4)
/SPI_SCK: U2.13 (SCL), U7.29 (PA5)
/STAT_LED: R13.1, U7.97 (PE0)
/SWDCLK: J19.2, U7.76 (PA14(JTCK)
/SWDIO: J19.1, U7.72 (PA13(JTMS)
/UART2_RX: J4.4, U7.25 (PA3)
/UART2_TX: J4.3, U7.24 (PA2)
/UART3_RX: J6.4, U7.56 (PD9)
/UART3_TX: J6.3, U7.55 (PD8)
/UART4_RX: J8.4, U7.23 (PA1)
/UART4_TX: J8.3, U7.22 (PA0)
/UART7_RX: J17.4, U7.37 (PE7)
/UART7_TX: J17.3, U7.38 (PE8)
/USB_+: J1.A6 (D+), J1.B6 (D+), R21.1
/USB_-: J1.A7 (D-), J1.B7 (D-), R20.2
/V_BCKP: BT1.1 (+), C8.1, R3.2, U4.6 (V_BCKP); also elsewhere on the board
GND: BT1.2 (-), BZ1.2 (-), C1.2, C2.2, C3.2, C4.2, C5.2, C6.2, C7.2, C8.2, C9.2, C10.2, C11.1, C12.2, C13.2, C14.2, C15.2, C16.2, C17.2, C18.2, C19.2, C20.2, C21.2, C24.2, C25.2, C26.2, C27.2, C28.2, C29.2, C30.2, C31.2, C32.2, C33.2, C34.2, C35.2, C36.2, C37.2, C38.2, C39.1, D2.1 (K), D3.1 (K), D4.1 (K), J1.A1 (GND), J1.A12 (GND), J1.B1 (GND), J1.B12 (GND), J1.S1 (SHIELD), J2.2, J3.2 (Ext), J4.2, J5.2, J6.2, J7.2, J8.2, J9.2, J10.2, J11.6 (VSS), J11.11 (SHIELD), J12.3, J13.3, J14.3, J15.3, J16.2, J17.2, J18.2, R1.2, R2.1, R5.2, R7.2, R9.2, R11.2, R12.2, R16.2, R19.2, R30.2, RESET1.1, SET1.1, U1.3 (VSS), U1.5 (SDO), U1.8 (VSS), U1.9 (VSS), U2.2 (SDx), U2.3 (SCx), U2.6 (GND), U2.7 (GND), U3.9 (GND), U3.11 (GND), U4.1 (GND), U4.10 (GND), U4.12 (GND), U5.9 (ST), U5.12 (GND), U6.1 (GND), U7.10 (VSS), U7.19 (VSSA), U7.26 (VSS), U7.49 (VSS), U7.74 (VSS), U7.99 (VSS), Y2.2, Y2.4; also elsewhere on the board
unnamed: BZ1.1 (+), R28.2
unnamed: C15.1, U7.48 (VCAP)
unnamed: C17.1, U7.73 (VCAP)
unnamed: D1.1 (K), R3.1
unnamed: D2.2 (A), R13.2
unnamed: D3.2 (A), R14.2
unnamed: D4.2 (A), R15.2
unnamed: J1.A5 (CC1), R1.1
unnamed: J1.B5 (CC2), R2.2
unnamed 64: J3.1 (In), U4.11 (RF_IN); also elsewhere on the board
unnamed: C5.1, U3.10 (CAP)
unnamed: R10.2, R11.1, U5.3 (CP2)
unnamed: R12.1, U5.10 (ILIM)
unnamed: R4.2, R5.1, U5.5 (OV1)
unnamed: R6.2, R7.1, U5.4 (OV2)
unnamed: R8.2, R9.1, U5.6 (PR1)
unnamed: C12.1, U5.11 (SS)
unnamed: C22.2, U6.6 (BST)
unnamed: C23.2, R18.2, R19.1, U6.4 (FB)
unnamed: C22.1, L1.1, U6.2 (SW)
unnamed: R20.1, U7.70 (PA11)
unnamed: R21.2, U7.71 (PA12)
unnamed: FB1.2, U7.21 (VDDA)
unnamed: R17.2, U7.20 (VREF+)
unnamed 79: TP1.1, U4.18 (~SAFEBOOT); also elsewhere on the board
VBUS: J1.A4 (VBUS), J1.A9 (VBUS), J1.B4 (VBUS), J1.B9 (VBUS), R4.1, R8.1, U5.7 (IN1)
VDD: C16.1, U5.1 (OUT), U5.8 (OUT__2), U6.3 (IN), U6.5 (EN)

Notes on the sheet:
Microcontroller
Micro SD Connector
Power MUX
Status LEDs
Magnetometer
Oscillators
Buzzer
ESC Power Terminals
Accelerometer/Gyroscope
Buttons
UART Connectors
ESC Headers
Pressure Sensor
Debug Header
Buck Regulator
Power Terminals
I2C Headers
USB C Connector
GPS Module

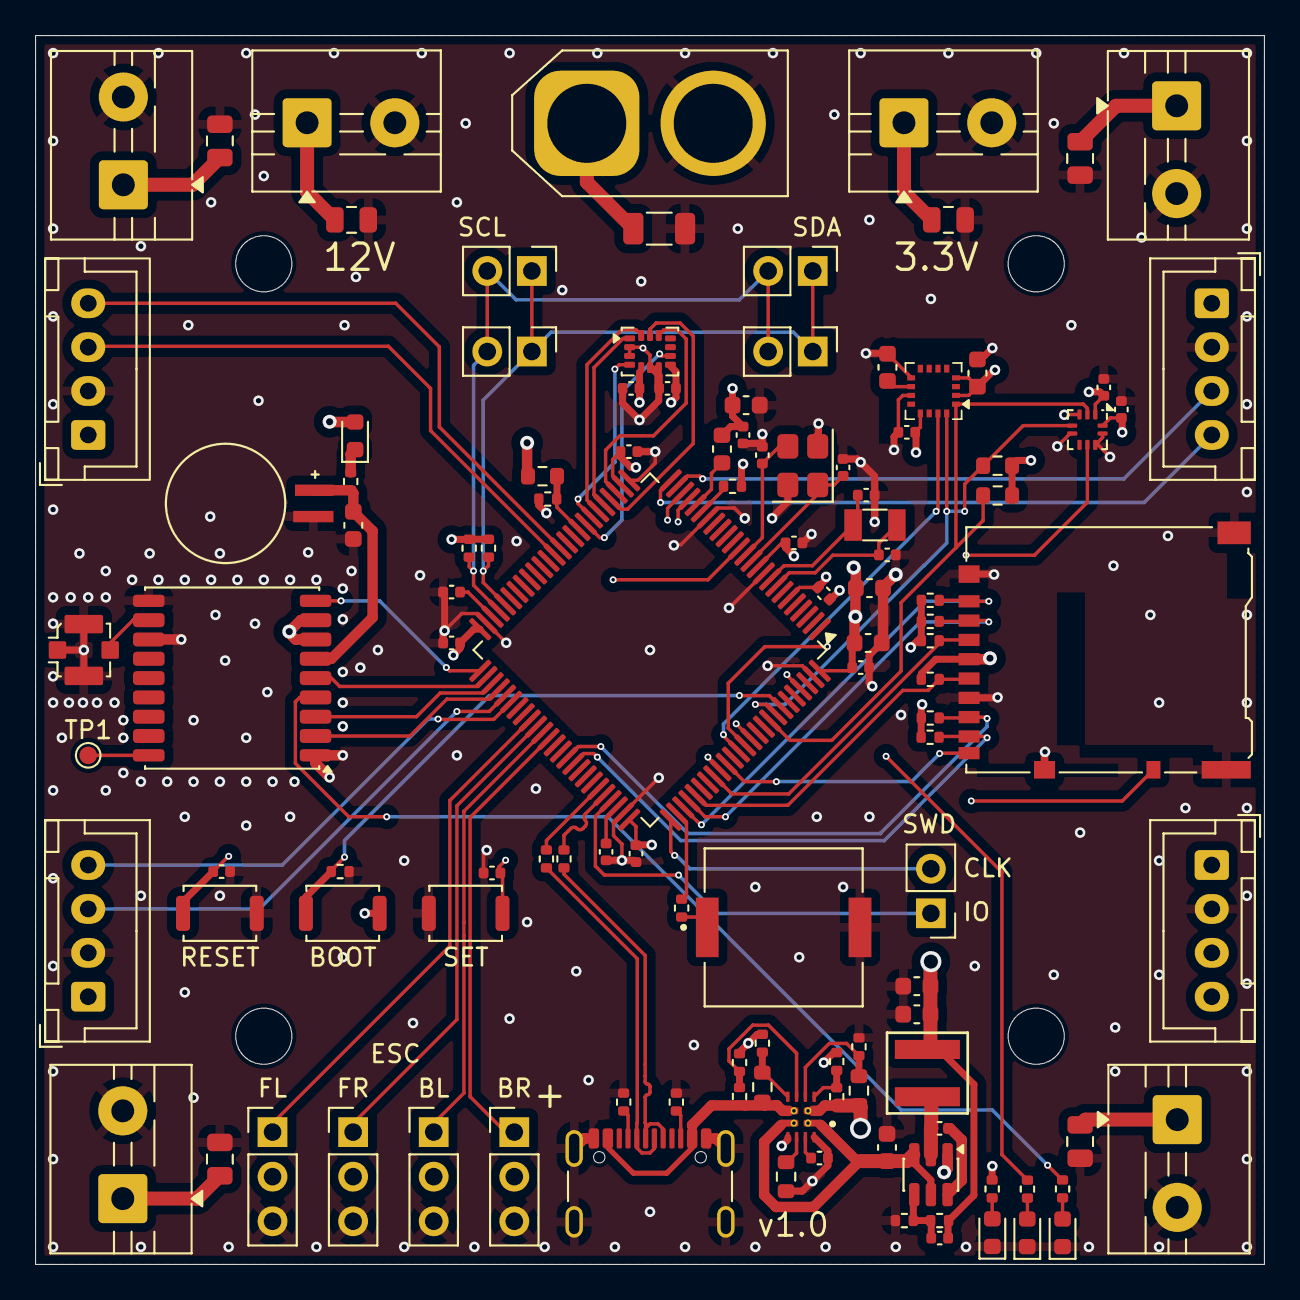
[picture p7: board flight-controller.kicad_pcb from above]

Board: 4 copper layers, 70.0 x 70.0 mm, 117 parts (0 on the bottom side), 82 nets.

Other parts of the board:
U8: MAX-M10S; ublox_MAX

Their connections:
+3.3V: U8.7 (VCC_IO), U8.8 (VCC); also elsewhere on the board
/GPS_INT: U8.5 (EXTINT); also elsewhere on the board
/GPS_LED: U8.4 (TIMEPULSE); also elsewhere on the board
/GPS_RESET: U8.9 (~RESET); also elsewhere on the board
/GPS_RX: U8.2 (TXD); also elsewhere on the board
/GPS_TX: U8.3 (RXD); also elsewhere on the board
/V_BCKP: U8.6 (V_BCKP); also elsewhere on the board
GND: U8.1 (GND), U8.10 (GND), U8.12 (GND); also elsewhere on the board
unnamed 64: U8.11 (RF_IN); also elsewhere on the board
unnamed 79: U8.18 (~SAFEBOOT); also elsewhere on the board

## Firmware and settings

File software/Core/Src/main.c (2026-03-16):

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
/* Includes ------------------------------------------------------------------*/
#include "main.h"
#include "fatfs.h"

/* USER CODE BEGIN Includes */

#include "ff.h"
#include "pid.h"
#include "uart.h"
#include "sdmmc.h"
#include "sensor.h"
#include "stm32h723xx.h"
#include "stm32h7xx_hal.h"
#include "stm32h7xx_hal_def.h"
#include "stm32h7xx_hal_i2c.h"
#include "stm32h7xx_hal_spi.h"
#include "stm32h7xx_hal_tim.h"
#include "stm32h7xx_hal_uart.h"
#include <stdint.h>

/* USER CODE END Includes */

/* USER CODE BEGIN PD */

#define DT 10

/* USER CODE END PD */

ADC_HandleTypeDef hadc1;

I2C_HandleTypeDef hi2c1;
I2C_HandleTypeDef hi2c2;

SD_HandleTypeDef hsd1;

SPI_HandleTypeDef hspi1;

TIM_HandleTypeDef htim4;

UART_HandleTypeDef huart4;
UART_HandleTypeDef huart7;
UART_HandleTypeDef huart1;
UART_HandleTypeDef huart2;
UART_HandleTypeDef huart3;

PCD_HandleTypeDef hpcd_USB_OTG_HS;

/* USER CODE BEGIN PV */

FATFS fatfs;
char sd_path[4];

// IMU PV
stmdev_ctx_t imu_h;

// MAG PV
MMC5983_HW_InitTypeDef mag_h = {
	.I2C_handler = &hi2c1,
	.I2C_Timeout = HAL_TIMEOUT
};

// BMP PV
bmp384_handle_t bmp_h;

// GNSS PV
GNSS_StateHandle gnss_h;

// Sensor PV
vector_t gyro;
vector_t accel;
vector_t mag;
float imu_temp;
float mag_temp;
float pressure;
float temp;

// PID PV
pid_control_t pid_x = {
	1,
	0,
	0
};
pid_control_t pid_y = {
	1,
	0,
	0
};
pid_control_t pid_z = {
	0.1,
	0,
	0
};

// AHRS PV
ahrs_t ahrs;

// Input PV
float throttle;
float set_x;
float set_y;
float set_z;

// Transceiver PV
uint8_t control_buf[sizeof(controls)];
uint8_t control_data;
int control_count = 0;

/* USER CODE END PV */

void SystemClock_Config(void);
static void MPU_Config(void);
static void MX_GPIO_Init(void);
static void MX_I2C1_Init(void);
static void MX_SDMMC1_SD_Init(void);
static void MX_SPI1_Init(void);
static void MX_UART4_Init(void);
static void MX_USART2_UART_Init(void);
static void MX_USB_OTG_HS_PCD_Init(void);
static void MX_ADC1_Init(void);
static void MX_TIM4_Init(void);
static void MX_USART3_UART_Init(void);
static void MX_USART1_UART_Init(void);
static void MX_UART7_Init(void);
static void MX_I2C2_Init(void);
/* USER CODE BEGIN PFP */

// ESC functions
static void esc_set_all(uint32_t duty_cycle);
static void esc_calibrate();
static void esc_start_all();
static void esc_stop_all();

static float clamp(float value, float min, float max);

/* USER CODE END PFP */

/**
 * @brief  The application entry point.
 * @retval int
 */
int main(void)
{

	/* USER CODE BEGIN 1 */

	imu_h.write_reg = platform_write;
	imu_h.read_reg = platform_read;
	imu_h.mdelay = platform_delay;
	imu_h.handle = &hspi1;

	bmp_h.iic_init = bmp384_interface_iic_init;
	bmp_h.iic_deinit = bmp384_interface_iic_deinit;
	bmp_h.iic_read = bmp384_interface_iic_read;
	bmp_h.iic_write = bmp384_interface_iic_write;
	bmp_h.delay_ms = HAL_Delay;

	/* USER CODE END 1 */

	/* MPU Configuration--------------------------------------------------------*/
	MPU_Config();

	/* MCU Configuration--------------------------------------------------------*/

	/* Reset of all peripherals, Initializes the Flash interface and the Systick. */
	HAL_Init();

	/* Configure the system clock */
	SystemClock_Config();

	/* Initialize all configured peripherals */
	MX_GPIO_Init();
	MX_I2C1_Init();
	MX_SDMMC1_SD_Init();
	MX_SPI1_Init();
	MX_UART4_Init();
	MX_USART2_UART_Init();
	MX_USB_OTG_HS_PCD_Init();
	MX_ADC1_Init();
	MX_TIM4_Init();
	MX_USART3_UART_Init();
	MX_USART1_UART_Init();
	MX_UART7_Init();
	MX_I2C2_Init();
	MX_FATFS_Init();
	/* USER CODE BEGIN 2 */

	sd_init(&fatfs, sd_path);

	// IMU Init
	platform_delay(LSM6DSO_BOOT_TIME);

	uint8_t whoami, rst;
	if (lsm6dso_device_id_get(&imu_h, &whoami) != LSM6DSO_ID) {
		sd_log("ERROR", "LSM6DSO", "Device id invalid or missing");
		Error_Handler();
	}

	lsm6dso_reset_set(&imu_h, PROPERTY_ENABLE);

	do {
		lsm6dso_reset_get(&imu_h, &rst);
	} while (rst);

	imu_init(&imu_h);

	// MAG Init
	if (MMC5983_ID_Verify(&mag_h) != MMC_NO_ERROR) {
		sd_log("ERROR", "MMC5983", "Device id invalid or missing");
		Error_Handler();
	}

	mag_init(&mag_h);

	// BMP Init
	if (bmp_init(&bmp_h) != 0) {
		sd_log("ERROR", "BMP384", "Device id invalid or missing");
		Error_Handler();
	}

	// GNSS Init
	GNSS_Init(&gnss_h, &huart1);
	HAL_Delay(1000);
	GNSS_LoadConfig(&gnss_h);

	esc_start_all();

	/* USER CODE END 2 */

	/* Infinite loop */
	/* USER CODE BEGIN WHILE */
	uint32_t gnss_timer = HAL_GetTick();
	uint32_t telemetry_timer = HAL_GetTick();
	ahrs.start_timestamp = HAL_GetTick();
	while (1)
	{
		/* USER CODE END WHILE */

		/* USER CODE BEGIN 3 */
		uint32_t timestamp = HAL_GetTick();

		// Poll data every second since gnss module doesn't have an interrupt pin
		if ((HAL_GetTick() - gnss_timer) > 1000) {
			read_gnss(&gnss_h);
			gnss_timer = HAL_GetTick();
		}

		// Send telemetry every 100 milliconds
		if ((HAL_GetTick() - telemetry_timer) > 100) {
			transmit_telemetry();
			telemetry_timer = HAL_GetTick();
		}

		// Run loop only if new imu data is available
		lsm6dso_status_reg_t status;
		do {
			lsm6dso_status_reg_get(&imu_h, &status);
		} while (!status.gda || !status.xlda);

		read_imu(&imu_h, &gyro, &accel, &imu_temp, status);

		update_ahrs(&ahrs, gyro, accel, mag, DT);
		vector_t orientation_euler = quaternion_to_euler(ahrs.orientation);

		float pid_x_out = loop_pid(&pid_x, orientation_euler.x, set_x);
		float pid_y_out = loop_pid(&pid_y, orientation_euler.y, set_y);
		float pid_z_out = loop_pid(&pid_z, orientation_euler.z, set_z);

		// Write duty cycle to ESCs
		TIM4->CCR1 = clamp(throttle + pid_x_out + pid_y_out - pid_z_out, 0, 100);
		TIM4->CCR2 = clamp(throttle - pid_x_out + pid_y_out + pid_z_out, 0, 100);
		TIM4->CCR3 = clamp(throttle + pid_x_out - pid_y_out + pid_z_out, 0, 100);
		TIM4->CCR4 = clamp(throttle - pid_x_out - pid_y_out - pid_z_out, 0, 100);

		// Delay to keep DT constant
		uint32_t time_elapsed = HAL_GetTick() - timestamp;
		HAL_Delay(time_elapsed);
	}
	/* USER CODE END 3 */
}

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
/* USER CODE BEGIN 4 */

void HAL_UART_RxCpltCallback(UART_HandleTypeDef *huart) {
	if (huart == &transceiver_h) {
		if (control_data == '\n') {
			controls = *(controls_t *)&control_buf;
			control_count = 0;
		} else {
			control_buf[control_count++] = control_data;
		}
		HAL_UART_Receive_IT(&transceiver_h, &control_data, 1);
	}
}

void HAL_GPIO_EXTI_Callback(uint16_t GPIO_Pin) {
	if(GPIO_Pin == MMC5983_INT_PIN){
		read_mag(&mag_h, &mag);
	}

	if (GPIO_Pin == BMP384_INT_PIN) {
		read_bmp(&bmp_h, &pressure, &temp);
	}
}

static void esc_start_all() {
	HAL_TIM_PWM_Start(&htim4, 1);
	HAL_TIM_PWM_Start(&htim4, 2);
	HAL_TIM_PWM_Start(&htim4, 3);
	HAL_TIM_PWM_Start(&htim4, 4);
}

static void esc_stop_all() {
	HAL_TIM_PWM_Stop(&htim4, 1);
	HAL_TIM_PWM_Stop(&htim4, 2);
	HAL_TIM_PWM_Stop(&htim4, 3);
	HAL_TIM_PWM_Stop(&htim4, 4);
}

static void esc_set_all(uint32_t duty_cycle) {
	TIM4->CCR1 = duty_cycle;
	TIM4->CCR2 = duty_cycle;
	TIM4->CCR3 = duty_cycle;
	TIM4->CCR4 = duty_cycle;
}

static void esc_calibrate() {
	esc_set_all(100);
	HAL_Delay(2);

	esc_set_all(50);
	HAL_Delay(1);

	esc_set_all(0);
}

static float clamp(float value, float min, float max) {
	if (value < min) {
		return min;
	}

	if (value > max) {
		return max;
	}

	return value;
}

I2C_HandleTypeDef get_hi2c_bmp() {
	return hi2c1;
}

float get_timestamp() {
	return HAL_GetTick();
}

/* USER CODE END 4 */

/* MPU Configuration */

void MPU_Config(void)
{
	MPU_Region_InitTypeDef MPU_InitStruct = {0};

	/* Disables the MPU */
	HAL_MPU_Disable();

	/** Initializes and configures the Region and the memory to be protected
	 */
	MPU_InitStruct.Enable = MPU_REGION_ENABLE;
	MPU_InitStruct.Number = MPU_REGION_NUMBER0;
	MPU_InitStruct.BaseAddress = 0x0;
	MPU_InitStruct.Size = MPU_REGION_SIZE_4GB;
	MPU_InitStruct.SubRegionDisable = 0x87;
	MPU_InitStruct.TypeExtField = MPU_TEX_LEVEL0;
	MPU_InitStruct.AccessPermission = MPU_REGION_NO_ACCESS;
	MPU_InitStruct.DisableExec = MPU_INSTRUCTION_ACCESS_DISABLE;
	MPU_InitStruct.IsShareable = MPU_ACCESS_SHAREABLE;
	MPU_InitStruct.IsCacheable = MPU_ACCESS_NOT_CACHEABLE;
	MPU_InitStruct.IsBufferable = MPU_ACCESS_NOT_BUFFERABLE;

	HAL_MPU_ConfigRegion(&MPU_InitStruct);
	/* Enables the MPU */
	HAL_MPU_Enable(MPU_PRIVILEGED_DEFAULT);

}

/**
 * @brief  This function is executed in case of error occurrence.
 * @retval None
 */
void Error_Handler(void)
{
	/* USER CODE BEGIN Error_Handler_Debug */
	/* User can add his own implementation to report the HAL error return state */
	__disable_irq();
	sd_log("FATAL", "Main", "Fatal error encountered rebooting");
	NVIC_SystemReset();
	/*
	   while (1)
	   {

	   }
	 */
	/* USER CODE END Error_Handler_Debug */
}
#ifdef USE_FULL_ASSERT
/**
 * @brief  Reports the name of the source file and the source line number
 *         where the assert_param error has occurred.
 * @param  file: pointer to the source file name
 * @param  line: assert_param error line source number
 * @retval None
 */
void assert_failed(uint8_t *file, uint32_t line)
{
	/* USER CODE BEGIN 6 */
	/* User can add his own implementation to report the file name and line number,
	   ex: printf("Wrong parameters value: file %s on line %d\r\n", file, line) */
	/* USER CODE END 6 */
}
#endif /* USE_FULL_ASSERT */

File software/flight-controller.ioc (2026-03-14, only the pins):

Mcu.UserName=STM32H723VGTx
PA0.Signal=UART4_TX
PA1.Signal=UART4_RX
PA11.Signal=USB_OTG_HS_DM
PA12.Signal=USB_OTG_HS_DP
PA13(JTMS/SWDIO).Signal=DEBUG_JTMS-SWDIO
PA14(JTCK/SWCLK).Signal=DEBUG_JTCK-SWCLK
PA15(JTDI).Signal=GPIO_Output
PA2.Signal=USART2_TX
PA3.Signal=USART2_RX
PA4.Signal=SPI1_NSS
PA5.Signal=SPI1_SCK
PA6.Signal=SPI1_MISO
PA7.Signal=SPI1_MOSI
PB0.Signal=ADCx_INP9
PB10.Signal=I2C2_SCL
PB11.Signal=I2C2_SDA
PB12.Signal=GPIO_Output
PB13.Signal=EVENTOUT
PB14.Signal=USART1_TX
PB15.Signal=USART1_RX
PB3(JTDO/TRACESWO).Signal=GPIO_Input
PB6.Signal=I2C1_SCL
PB7.Signal=I2C1_SDA
PC10.Signal=SDMMC1_D2
PC11.Signal=SDMMC1_D3
PC12.Signal=SDMMC1_CK
PC14-OSC32_IN.Signal=RCC_OSC32_IN
PC15-OSC32_OUT.Signal=RCC_OSC32_OUT
PC4.Signal=GPXTI4
PC5.Signal=GPXTI5
PC8.Signal=SDMMC1_D0
PC9.Signal=SDMMC1_D1
PD12.Signal=S_TIM4_CH1
PD13.Signal=S_TIM4_CH2
PD14.Signal=S_TIM4_CH3
PD15.Signal=S_TIM4_CH4
PD2.Signal=SDMMC1_CMD
PD3.Signal=GPIO_Input
PD4.Signal=GPIO_Input
PD6.Signal=GPXTI6
PD7.Signal=GPXTI7
PD8.Signal=USART3_TX
PD9.Signal=USART3_RX
PE0.Signal=GPIO_Output
PE7.Signal=UART7_RX
PE8.Signal=UART7_TX
PH0-OSC_IN.Signal=RCC_OSC_IN
PH1-OSC_OUT.Signal=RCC_OSC_OUT

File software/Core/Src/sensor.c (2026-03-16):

#include "main.h"
#include "GNSS.h"
#include "sensor.h"
#include "driver_bmp384.h"
#include "driver_bmp384_interface.h"
#include "lsm6dso_reg.h"
#include "stm32h7xx_hal.h"
#include "stm32h7xx_hal_def.h"
#include "stm32h7xx_hal_i2c.h"
#include <string.h>

void imu_init(stmdev_ctx_t *imu_h) {
	/* Disable I3C interface */
	lsm6dso_i3c_disable_set(imu_h, LSM6DSO_I3C_DISABLE);

	/* Enable Block Data Update */
	lsm6dso_block_data_update_set(imu_h, PROPERTY_ENABLE);

	/* Set Output Data Rate */
	lsm6dso_xl_data_rate_set(imu_h, LSM6DSO_XL_ODR_6667Hz);
	lsm6dso_gy_data_rate_set(imu_h, LSM6DSO_GY_ODR_6667Hz);

	/* Set full scale */
	lsm6dso_xl_full_scale_set(imu_h, LSM6DSO_4g);
	lsm6dso_gy_full_scale_set(imu_h, LSM6DSO_2000dps);

	/* Configure filtering chain(No aux interface)
	 * Accelerometer - LPF1 + LPF2 path
	 */
	lsm6dso_xl_hp_path_on_out_set(imu_h, LSM6DSO_LP_ODR_DIV_100);
	lsm6dso_xl_filter_lp2_set(imu_h, PROPERTY_ENABLE);
}

void read_imu(stmdev_ctx_t *imu_h, vector_t *accel, vector_t *gyro, float *imu_temp, lsm6dso_status_reg_t status) {
	int16_t gyro_raw[3], accel_raw[3], imu_temp_raw;

	if (status.xlda) {
		/* Read acceleration field data */
		memset(accel_raw, 0x00, 3 * sizeof(int16_t));
		lsm6dso_acceleration_raw_get(imu_h, accel_raw);
		accel->x = lsm6dso_from_fs2_to_mg(accel_raw[0]);
		accel->y = lsm6dso_from_fs2_to_mg(accel_raw[1]);
		accel->z = lsm6dso_from_fs2_to_mg(accel_raw[2]);
	}

	if (status.gda) {
		/* Read angular rate field data */
		memset(gyro_raw, 0x00, 3 * sizeof(int16_t));
		lsm6dso_angular_rate_raw_get(imu_h, gyro_raw);
		gyro->x = lsm6dso_from_fs2000_to_mdps(gyro_raw[0]);
		gyro->y = lsm6dso_from_fs2000_to_mdps(gyro_raw[1]);
		gyro->z = lsm6dso_from_fs2000_to_mdps(gyro_raw[2]);
	}

	if (status.tda) {
		/* Read temperature data */
		memset(&imu_temp_raw, 0x00, sizeof(int16_t));
		lsm6dso_temperature_raw_get(imu_h, &imu_temp_raw);
		*imu_temp = lsm6dso_from_lsb_to_celsius(imu_temp_raw);
	}
}

int32_t platform_write(void *handle, uint8_t reg, const uint8_t *bufp, uint16_t len) {
	if (HAL_SPI_Transmit(handle, &reg, 1, HAL_TIMEOUT) != HAL_OK) {
		return -1;
	}
	if (HAL_SPI_Transmit(handle, bufp, len, HAL_TIMEOUT) != HAL_OK) {
		return -1;
	}

	return 0;
}

int32_t platform_read(void *handle, uint8_t reg, uint8_t *bufp, uint16_t len) {
	if (HAL_SPI_Transmit(handle, &reg, 1, HAL_TIMEOUT) != HAL_OK) {
		return -1;
	}
	if (HAL_SPI_Receive(handle, bufp, len, HAL_TIMEOUT) != HAL_OK) {
		return -1;
	}

	return 0;
}

void platform_delay(uint32_t millisec) {
	HAL_Delay(millisec);
}

void mag_init(MMC5983_HW_InitTypeDef *mag_h) {
	MMC5983_Data_TypeDef mag_data;

	MMC5983_SW_Reset(mag_h);

	MMC5983_Set_Bandwidth(mag_h, MMC_BW_0400);
	MMC5983_Set_Operation_Rate(mag_h, MMC_SET_0500);
	MMC5983_Enable_Auto_Set_Reset(mag_h);
	MMC5983_Set_Output_DataRate(mag_h, MMC_ODR_0100);
	MMC5983_Set_Interrupt_Measurement(mag_h, &mag_data);
}

void read_mag(MMC5983_HW_InitTypeDef *mag_h, vector_t *mag) {
	MMC5983_Data_TypeDef mag_data;

	if (MMC5983_Data_Read(mag_h, &mag_data) == MMC_NO_ERROR) {
		mag->x = mag_data.axes.DX;
		mag->y = mag_data.axes.DY;
		mag->z = mag_data.axes.DZ;
	}
}

uint8_t bmp_init(bmp384_handle_t *bmp_h) {
	bmp384_set_interface(bmp_h, BMP384_INTERFACE_IIC);
	bmp384_set_addr_pin(bmp_h, BMP384_ADDRESS_ADO_LOW);

	if (bmp384_init(bmp_h) != 0) {
		return 1;
	}

	bmp384_set_iic_watchdog_timer(bmp_h, BMP384_BOOL_FALSE);
	bmp384_set_iic_watchdog_period(bmp_h, BMP384_IIC_WATCHDOG_PERIOD_1P25_MS);

	bmp384_set_fifo(bmp_h, BMP384_BOOL_FALSE);

	bmp384_set_interrupt_pin_type(bmp_h, BMP384_INTERRUPT_PIN_TYPE_PUSH_PULL);
	bmp384_set_interrupt_active_level(bmp_h, BMP384_INTERRUPT_ACTIVE_LEVEL_HIGHER);
	bmp384_set_latch_interrupt_pin_and_interrupt_status(bmp_h, BMP384_BOOL_FALSE);
	bmp384_set_interrupt_fifo_watermark(bmp_h, BMP384_BOOL_FALSE);
	bmp384_set_interrupt_fifo_full(bmp_h, BMP384_BOOL_FALSE);
	bmp384_set_interrupt_data_ready(bmp_h, BMP384_BOOL_TRUE);

	bmp384_set_pressure(bmp_h, BMP384_BOOL_TRUE);
	bmp384_set_temperature(bmp_h, BMP384_BOOL_TRUE);
	bmp384_set_pressure_oversampling(bmp_h, BMP384_OVERSAMPLING_x32);
	bmp384_set_temperature_oversampling(bmp_h, BMP384_OVERSAMPLING_x2);
	bmp384_set_odr(bmp_h, BMP384_ODR_100_HZ);
	bmp384_set_filter_coefficient(bmp_h, BMP384_FILTER_COEFFICIENT_3);
	bmp384_set_mode(bmp_h, BMP384_MODE_NORMAL_MODE);

	return 0;
}

void read_bmp(bmp384_handle_t *bmp_h, float *pressure, float *temp) {
	uint32_t pressure_raw, temp_raw;

	bmp384_read_temperature_pressure(bmp_h, &temp_raw, temp, &pressure_raw, pressure);
}

uint8_t bmp384_interface_iic_init() {
	return 0; // I2C should already be initialized
}

uint8_t bmp384_interface_iic_deinit() {
	return 0; // Shouldn't need to call this
}

uint8_t bmp384_interface_iic_read(uint8_t addr, uint8_t reg, uint8_t *buf, uint16_t len) {
	I2C_HandleTypeDef hi2c_bmp = get_hi2c_bmp();
	if (HAL_I2C_Mem_Read(&hi2c_bmp, addr, reg, 1, buf, len, HAL_TIMEOUT) != HAL_OK) {
		return 1;
	}

	return 0;
}

uint8_t bmp384_interface_iic_write(uint8_t addr, uint8_t reg, uint8_t *buf, uint16_t len) {
	I2C_HandleTypeDef hi2c_bmp = get_hi2c_bmp();
	if (HAL_I2C_Mem_Write(&hi2c_bmp, addr, reg, 1, buf, len, HAL_TIMEOUT) != HAL_OK) {
		return 1;
	}

	return 0;
}

void read_gnss(GNSS_StateHandle *gnss_h) {
	GNSS_GetUniqID(gnss_h);
	GNSS_ParseBuffer(gnss_h);

	HAL_Delay(250);

	GNSS_GetPVTData(gnss_h);
	GNSS_ParseBuffer(gnss_h);
}

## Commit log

2026-03-02 started schematic
    [flight-controller.kicad_pcb, flight-controller.kicad_sch]
2026-03-03 made schematic outline
    [flight-controller.kicad_sch]
2026-03-03 added gps
    [flight-controller.kicad_sch]
2026-03-06 worked on schematic
    [flight-controller.kicad_sch]
2026-03-07 routed schematic
    [flight-controller.kicad_sch]
2026-03-09 worked on layout
    [flight-controller.kicad_pcb, flight-controller.kicad_sch]
2026-03-09 added uart port and buzzer
    [flight-controller.kicad_pcb, flight-controller.kicad_sch]
2026-03-10 routing pcb
    [flight-controller.kicad_pcb, flight-controller.kicad_sch]
2026-03-10 added buzzer type
    [flight-controller.kicad_sch]
2026-03-10 isolated magnetometer
    [flight-controller.kicad_pcb]
2026-03-10 finished pcb
    [flight-controller.kicad_pcb]
2026-03-10 added 3d files
    [flight-controller.kicad_pcb]
2026-03-10 finished board
    [flight-controller.kicad_pcb, flight-controller.kicad_sch]
2026-03-11 added I2C pins
    [flight-controller.kicad_pcb, flight-controller.kicad_sch]
2026-03-11 added seperate I2C channel
    [flight-controller.kicad_sch]
2026-03-11 added pwm silkscreen
    [flight-controller.kicad_pcb]
2026-03-12 fixed usb plug
    [flight-controller.kicad_pcb, flight-controller.kicad_sch]
2026-03-12 added pid lib
2026-03-12 cleaning up
    [flight-controller.kicad_pcb]
2026-03-12 fixed kicad error
    [flight-controller.kicad_sch]
2026-03-13 updated silkscreen
    [flight-controller.kicad_pcb]
2026-03-13 changed int pins and fixed i2c
    [flight-controller.kicad_pcb, flight-controller.kicad_sch]
2026-03-14 added mag driver
2026-03-14 added pressure sensor driver
2026-03-14 added gnss driver
2026-03-14 added sd card and basic error handling
    [flight-controller.ioc, main.c, sensor.c]
2026-03-16 added i2c pullup resistors
    [flight-controller.kicad_pcb, flight-controller.kicad_sch]
2026-03-16 added lines to schematic
    [flight-controller.kicad_sch]
2026-03-17 added production files
    [bom.csv, designators.csv, positions.csv]
2026-03-17 replaced gps with max-m10s
    [bom.csv, designators.csv, flight-controller.kicad_pcb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]
2026-03-17 updated production files
    [designators.csv, positions.csv]
2026-03-17 touching up pcb
    [flight-controller.kicad_pcb]
2026-03-18 added silkscreen
    [flight-controller.kicad_pcb]
2026-03-18 updated pcb

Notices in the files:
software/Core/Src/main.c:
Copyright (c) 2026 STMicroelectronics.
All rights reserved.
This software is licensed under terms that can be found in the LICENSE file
